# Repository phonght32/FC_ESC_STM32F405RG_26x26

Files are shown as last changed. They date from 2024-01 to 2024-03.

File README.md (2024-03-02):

# FC_ESC_STM32F405RG_26x26

### 1. Overview

All-in-One (AIO) circuit for quadcopter. STM32F405 is the main controller for FC and EFM8BB21 is the main controller for ESC. Screw hole dimension is 26x26 mm that compatible for almost tiny drone frame. 

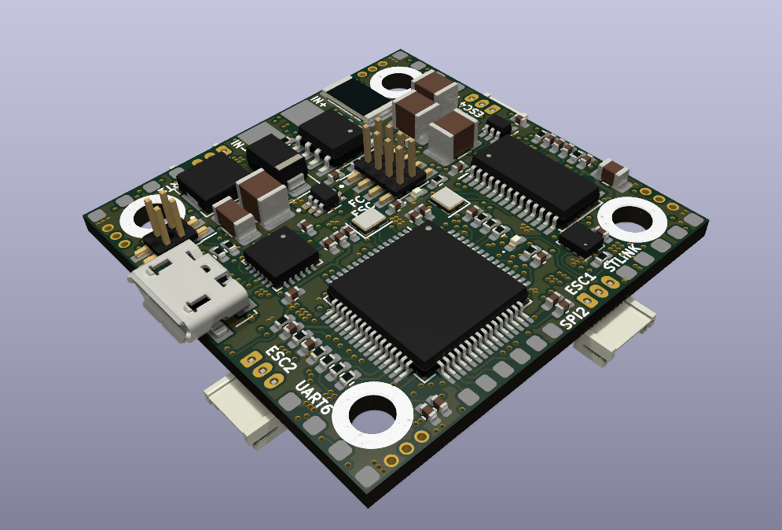
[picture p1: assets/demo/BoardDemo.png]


Everything about this board: Schematic, PCB gerber and BOM are free to distribute under open-source license for users.

### 2. Specifications

| Items | Specifications |
| --- | --- |
| Power supply | Pin LiPo 2-4 cell |
| Microcontroller | STM32F405RGT6 / 32-bit ARM Cortex-M4 with FPU(168MHz, 225DMIPS) |
| Sensors | MPU6000 (3 axis gyroscope, 3 axis accelerometer) <br />BMP280 (barometer)<br />INA186 (current) |
| Programmer | JTAG/SWD connector |
| Communicaton Ports  | UART x 4<br />I2C x 1<br />SPI x 1 |
| OSD | Built-in AT7456 |
| LEDs and Buttons | LED RED: 3V3 power on<br />LED BLUE: User status |
| Output power source | TPS5430 5V@5A<br />RT9013 3V3@500mA |
| Dimensions | 34 x34 mm<br />Screw hole 26 x 26 mm |

**NOTE:**

This board use jumper to select 5V power source and to enable 3V3 power supply.

### 3. Layout / Pin map

| Function | Pin |
| --- | --- |
| UART1 | PA9: TX<br />PA10: RX |
| UART3 | PB10: TX<br />PB11: RX |
| UART4 | PA0: TX<br />PA1: RX |
| UART6 | PC6: TX<br />PC7: RX |
| SPI2 | PB12: CS<br />PB13: CLK<br />PB14: MISO<br />PB15: MOSI |
| I2C2 | PB10: SCL<br />PB11: SDA |
| LED | LED status: PB7<br />LED strip: PB6 |
| BUZZER | PC13 |
| USB Port | D-: PA11<br />D+: PA12 |
| Measurement | Current sens: PC1<br />Voltage sens: PC2<br />USB voltage sens: PC5 |

### 4. Hardware design

#### Schematic

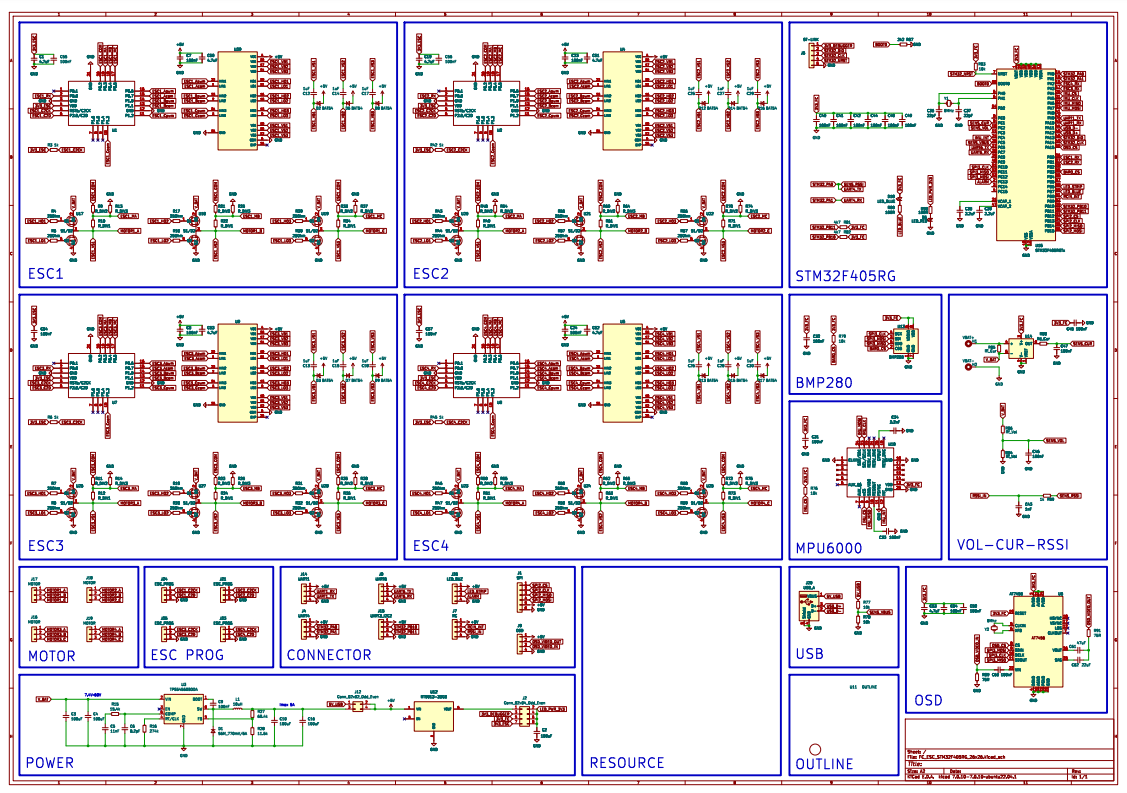
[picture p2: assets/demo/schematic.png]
schematic


#### PCB F.Cu

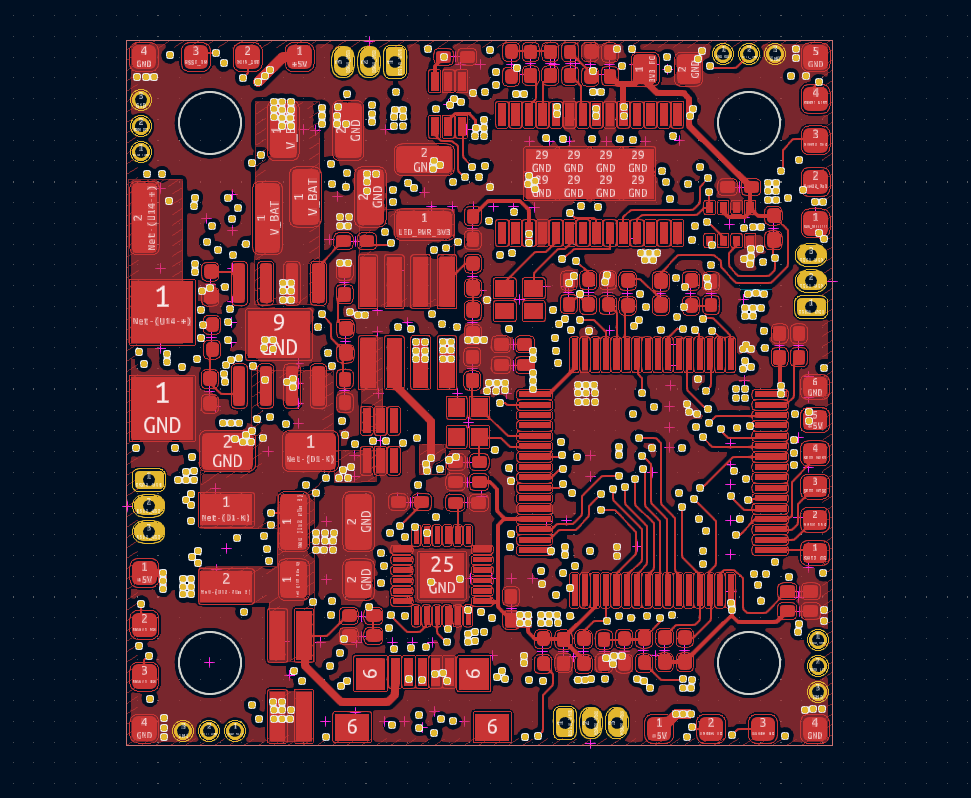
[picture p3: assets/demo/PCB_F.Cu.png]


#### PCB In1.Cu

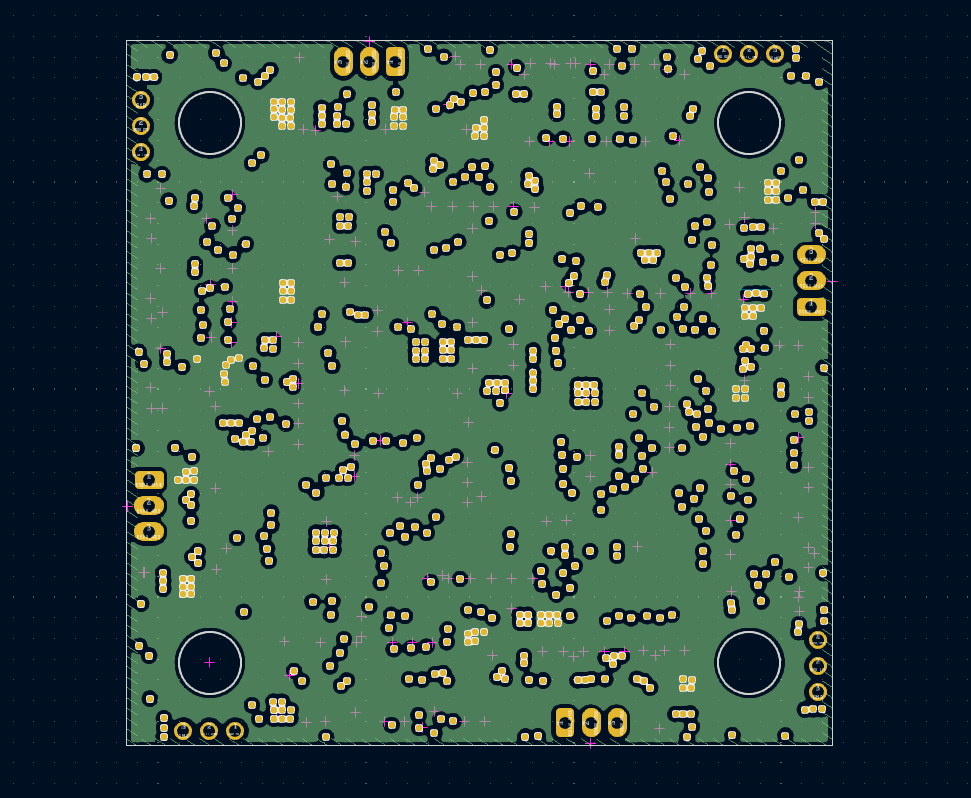
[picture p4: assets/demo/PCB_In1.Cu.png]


#### PCB In2.Cu

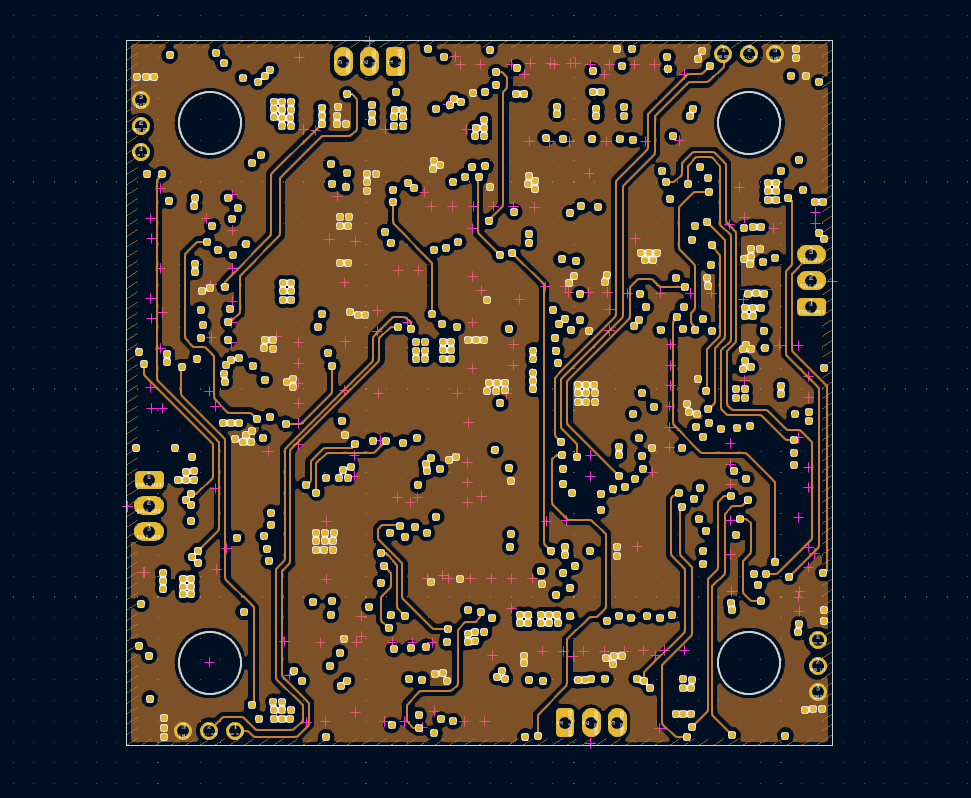
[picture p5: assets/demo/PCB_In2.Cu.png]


#### PCB In3.Cu

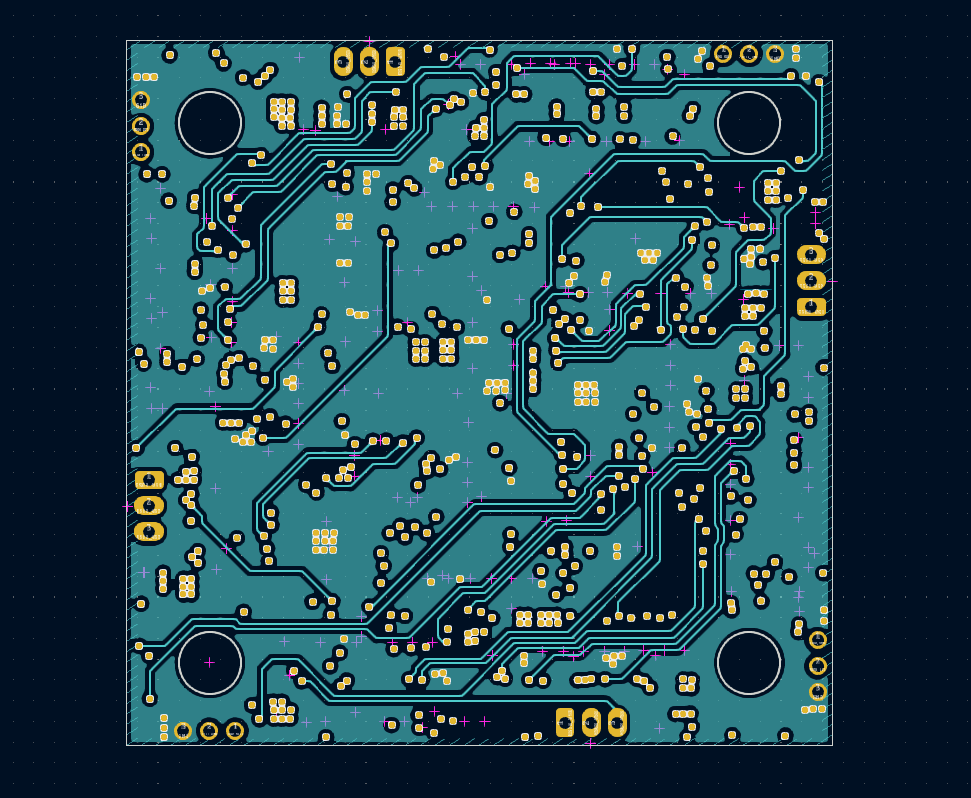
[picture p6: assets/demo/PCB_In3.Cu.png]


#### PCB In4.Cu

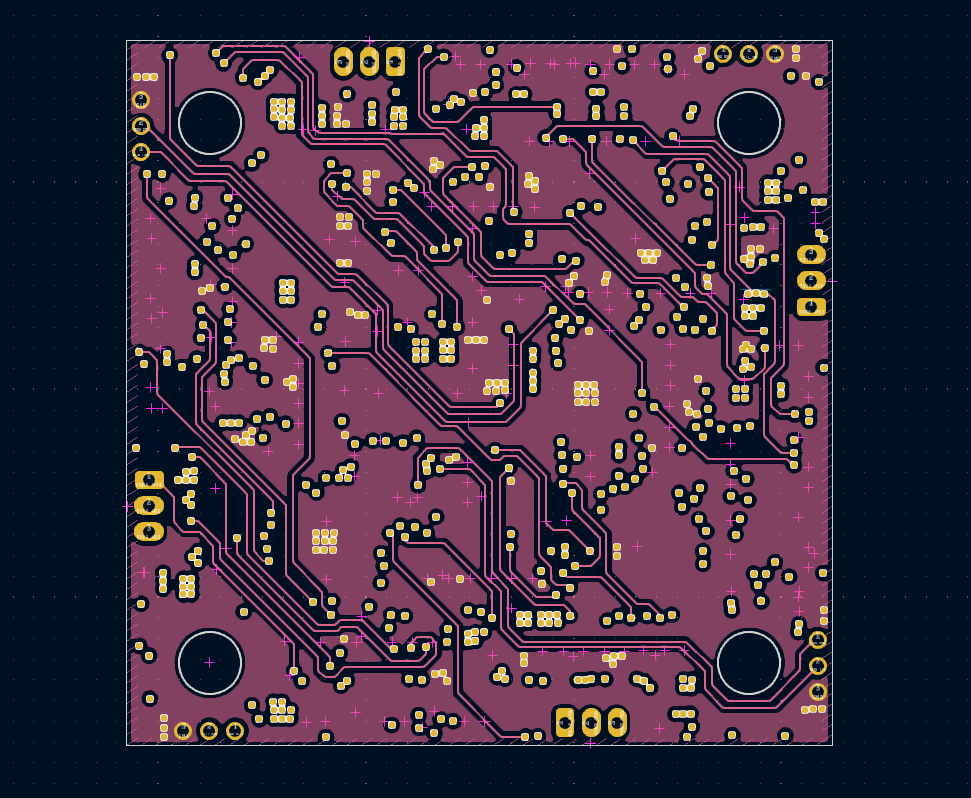
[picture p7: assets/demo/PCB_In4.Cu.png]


#### PCB In5.Cu

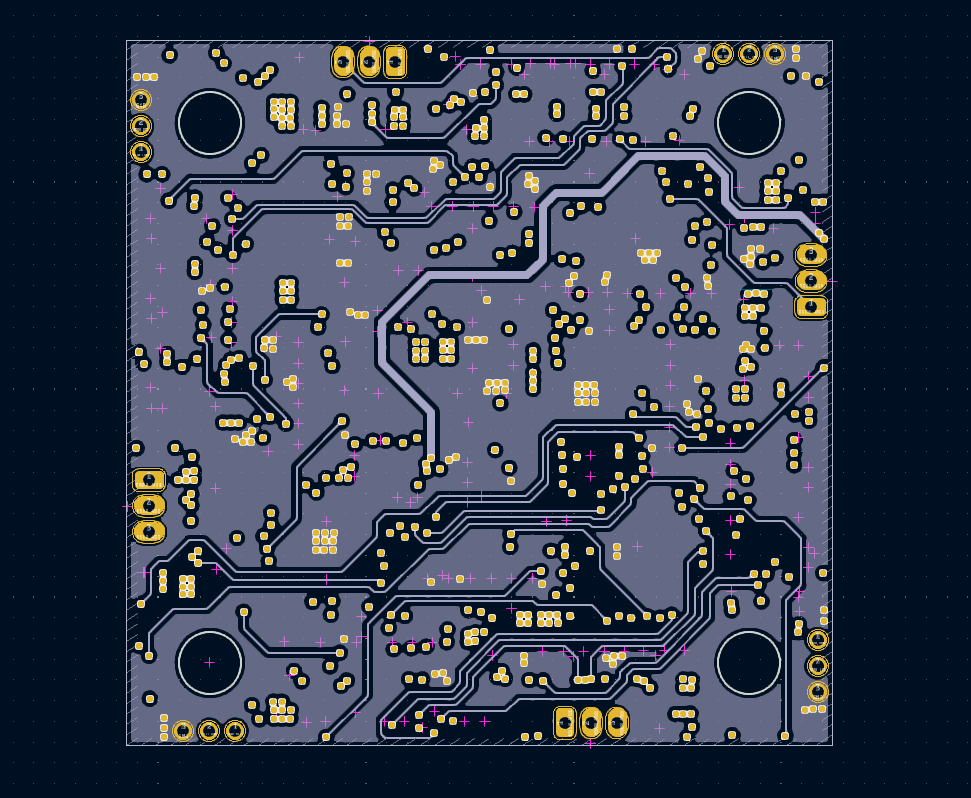
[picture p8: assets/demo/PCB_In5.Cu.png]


#### PCB In6.Cu

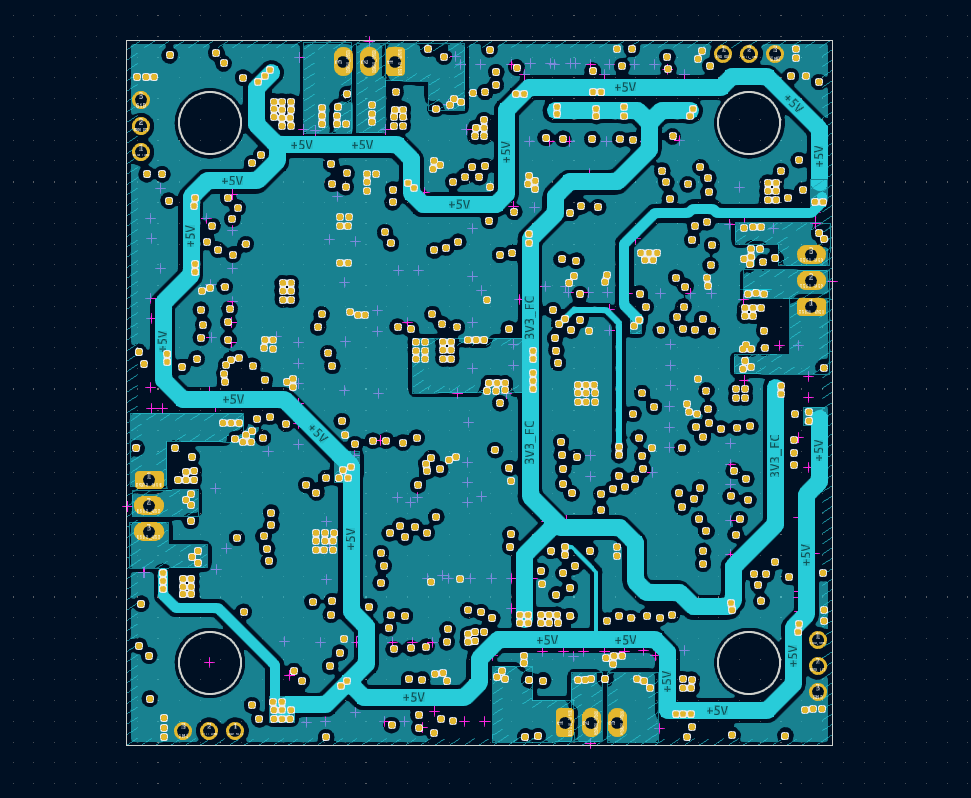
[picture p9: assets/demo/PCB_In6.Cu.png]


#### PCB B.Cu

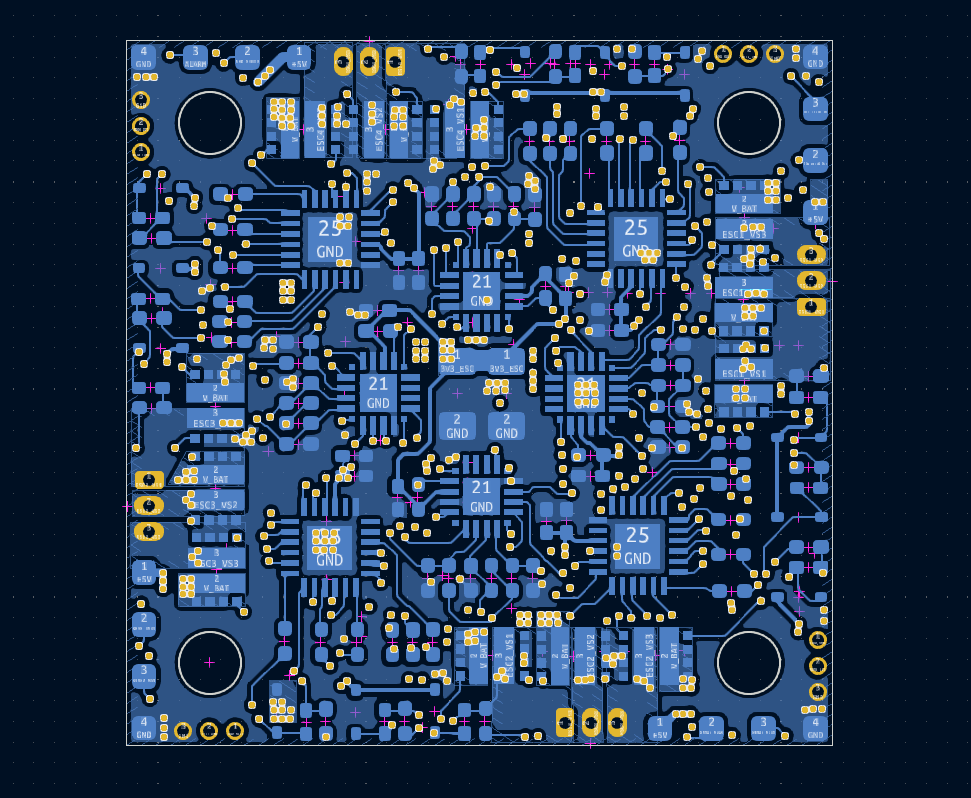
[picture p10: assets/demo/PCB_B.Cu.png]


#### Dimension

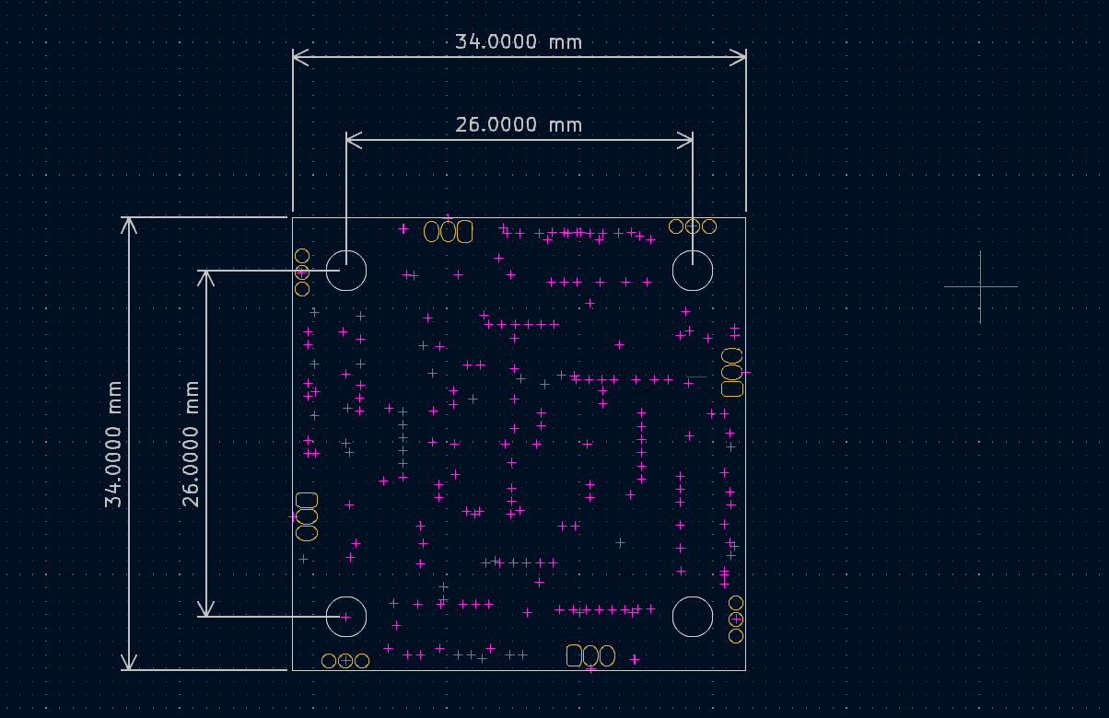
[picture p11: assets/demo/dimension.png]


#### 3D Top

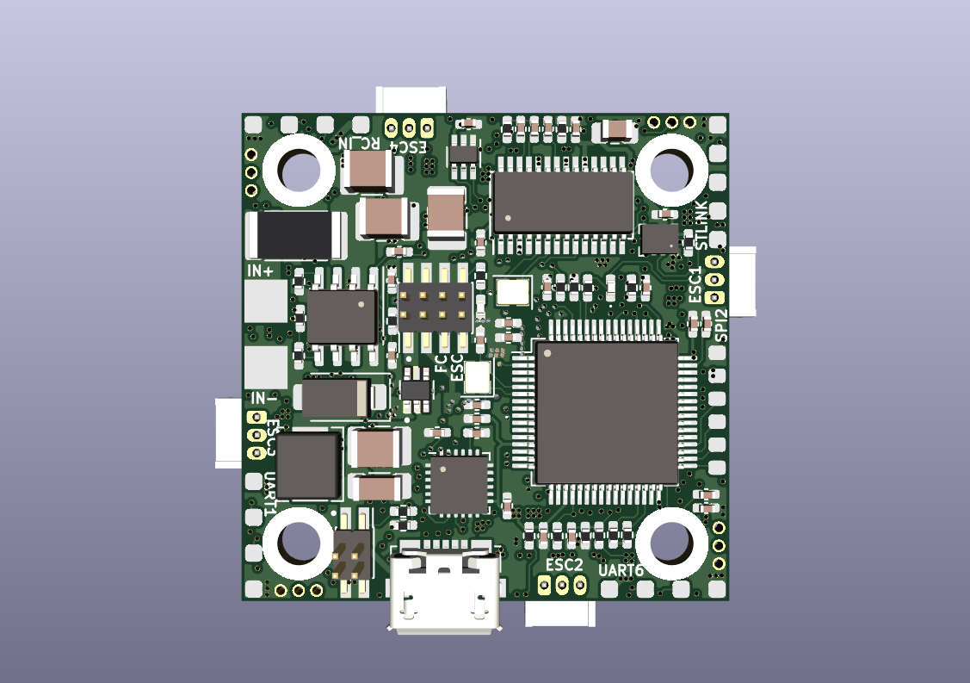
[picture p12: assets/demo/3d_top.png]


#### 3D Bot

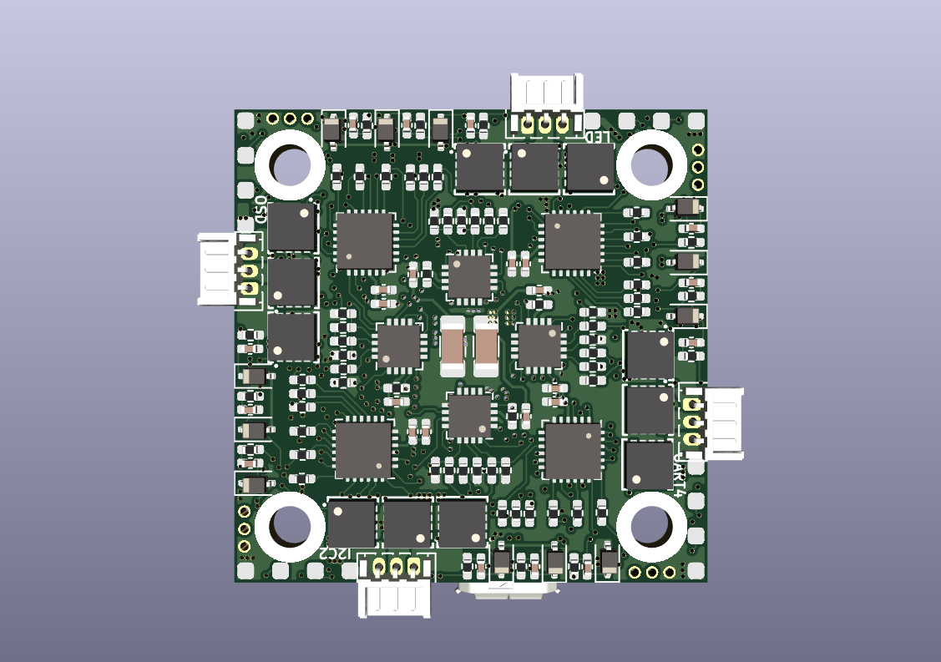
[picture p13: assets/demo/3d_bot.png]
3d_bot


### 5. Bill of Materials (BOM)

[Download.](assets/BOM/FC_ESC_STM32F405RG_26x26.xlsx)

### 6. Gerber

[Download.](assets/gerber_FC_ESC_STM32F405RG_26x26_v1_0.zip)

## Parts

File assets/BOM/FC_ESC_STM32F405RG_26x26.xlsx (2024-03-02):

Reference | Value | Footprint | Qty
C1,C19 | 4.7uF | Capacitor_SMD:C_1206_3216Metric_Pad1.33x1.80mm_HandSolder | 2
C2,C3,C4,C10 | 100uF | Capacitor_SMD:C_1210_3225Metric_Pad1.33x2.70mm_HandSolder | 4
C5 | 11nF | Capacitor_SMD:C_0402_1005Metric_Pad0.74x0.62mm_HandSolder | 1
C6 | 8.2pF | Capacitor_SMD:C_0402_1005Metric_Pad0.74x0.62mm_HandSolder | 1
C7,C8,C9,C23,C24,C31,C32,C33,C40,C41,C42,C44,C45,C46,C47,C48,C49,C54,C55,C56,C57,C59,C60,C64 | 100nF | Capacitor_SMD:C_0402_1005Metric_Pad0.74x0.62mm_HandSolder | 24
C12,C13,C14,C15,C17,C18,C25,C26,C27,C28,C29,C30 | 1uF | Capacitor_SMD:C_0402_1005Metric_Pad0.74x0.62mm_HandSolder | 12
C16 | 100uF | Capacitor_SMD:C_1206_3216Metric_Pad1.33x1.80mm_HandSolder | 1
C34 | 2.2nF | Capacitor_SMD:C_0402_1005Metric_Pad0.74x0.62mm_HandSolder | 1
C36,C37 | 22pF | Capacitor_SMD:C_0402_1005Metric_Pad0.74x0.62mm_HandSolder | 2
C38,C39 | 2.2uF | Capacitor_SMD:C_0402_1005Metric_Pad0.74x0.62mm_HandSolder | 2
C43 | 1nF | Capacitor_SMD:C_0402_1005Metric_Pad0.74x0.62mm_HandSolder | 1
C50,C51,C52,C53 | 4.7uF | Capacitor_SMD:C_0402_1005Metric_Pad0.74x0.62mm_HandSolder | 4
C61 | 47uF | Capacitor_SMD:C_0402_1005Metric_Pad0.74x0.62mm_HandSolder | 1
C62 | 22uF | Capacitor_SMD:C_0402_1005Metric_Pad0.74x0.62mm_HandSolder | 1
C63 | 4.7uF | Capacitor_SMD:C_0805_2012Metric_Pad1.18x1.45mm_HandSolder | 1
D1 | S6M_770mV/6A | Diode_SMD:D_SMA | 1
D2,D3,D6,D7,D8,D9,D12,D13,D14,D15,D16,D17 | BAT54 | Diode_SMD:D_SOD-323 | 12
D5 | LED_RED | LED_SMD:LED_0402_1005Metric_Pad0.77x0.64mm_HandSolder | 1
D18 | LED_BLUE | LED_SMD:LED_0402_1005Metric_Pad0.77x0.64mm_HandSolder | 1
H1 | VBAT+ | Proj_footprint:MoutingPad | 1
H2 | VBAT- | Proj_footprint:MoutingPad | 1
J1 | SPI | Proj_footprint:MountingPad_1x6 | 1
J2 | Conn_02x04_Odd_Even | Proj_footprint:PinHeader_2x04_P1.27mm_Vertical_SMD | 1
J4 | UART4 | Proj_footprint:MountingPad_1x4 | 1
J5 | ST-LINK | Proj_footprint:STLINK_Port | 1
J7 | RC | Proj_footprint:MountingPad_1x4 | 1
J8 | UART6 | Proj_footprint:MountingPad_1x4 | 1
J9 | OSD | Proj_footprint:MountingPad_1x4 | 1
J12 | Conn_02x02_Odd_Even | Proj_footprint:PinHeader_2x02_P1.27mm_Vertical_SMD | 1
J14 | UART1 | Proj_footprint:MountingPad_1x4 | 1
J15 | UART3_I2C2 | Proj_footprint:MountingPad_1x4 | 1
J16,J17,J18,J19 | MOTOR | Proj_footprint:Hirose_DF13-03P-1.25DS_1x03_P1.25mm_Horizontal | 4
J20 | USB_A | Proj_footprint:USB_Micro-B_SMD | 1
J21,J23,J24,J25 | ESC_PROG | Proj_footprint:ESC_Program | 4
J26 | LED_BUZ | Proj_footprint:MountingPad_1x4 | 1
L1 | 10uH | Proj_footprint:Inductor | 1
R3,R6,R42,R45,R89 | 1k | Resistor_SMD:R_0402_1005Metric_Pad0.72x0.64mm_HandSolder | 5
R4,R5,R7,R8,R17,R18,R19,R20,R29,R30,R31,R32,R43,R44,R46,R47,R56,R57,R58,R59,R66,R67,R68,R69 | 25Ohm | Resistor_SMD:R_0402_1005Metric_Pad0.72x0.64mm_HandSolder | 24
R9,R11,R21,R23,R33,R35,R48,R50,R60,R62,R70,R72 | R_DIV2 | Resistor_SMD:R_0402_1005Metric_Pad0.72x0.64mm_HandSolder | 12
R10,R12,R22,R24,R34,R36,R49,R51,R61,R63,R71,R73 | R_DIV1 | Resistor_SMD:R_0402_1005Metric_Pad0.72x0.64mm_HandSolder | 12
R13,R14,R25,R26,R37,R38,R54,R55,R64,R65,R74,R75 | R_DIV3 | Resistor_SMD:R_0402_1005Metric_Pad0.72x0.64mm_HandSolder | 12
R15 | 15.4k | Resistor_SMD:R_0402_1005Metric_Pad0.72x0.64mm_HandSolder | 1
R16 | 274k | Resistor_SMD:R_0402_1005Metric_Pad0.72x0.64mm_HandSolder | 1
R27 | 60.4k | Resistor_SMD:R_0402_1005Metric_Pad0.72x0.64mm_HandSolder | 1
R28 | 11.5k | Resistor_SMD:R_0402_1005Metric_Pad0.72x0.64mm_HandSolder | 1
R39,R91 | 75R | Resistor_SMD:R_0402_1005Metric_Pad0.72x0.64mm_HandSolder | 2
R76,R77,R78,R79,R83 | 10k | Resistor_SMD:R_0402_1005Metric_Pad0.72x0.64mm_HandSolder | 5
R80,R93 | 100R | Resistor_SMD:R_0402_1005Metric_Pad0.72x0.64mm_HandSolder | 2
R81,R82 | 4k7 | Resistor_SMD:R_0402_1005Metric_Pad0.72x0.64mm_HandSolder | 2
R84 | Ri_Vol | Resistor_SMD:R_0402_1005Metric_Pad0.72x0.64mm_HandSolder | 1
R85 | Ri_Cur | Resistor_SMD:R_2512_6332Metric | 1
R86 | Rf_Vol | Resistor_SMD:R_0402_1005Metric_Pad0.72x0.64mm_HandSolder | 1
R87 | 2k2 | Resistor_SMD:R_0402_1005Metric_Pad0.72x0.64mm_HandSolder | 1
R88 | Rd_Cur | Resistor_SMD:R_0402_1005Metric_Pad0.72x0.64mm_HandSolder | 1
U1,U2,U7,U8 | EFM8BB21 | Proj_footprint:QFN-20-1EP_3x3mm_P0.5mm_EP1.8x1.8mm | 4
U3 | TPS54560BDDA | Proj_footprint:SOIC-8-1EP_3.9x4.9mm_P1.27mm_EP2.29x3mm | 1
U4,U5,U9,U29 | FD6288Q | Proj_footprint:QFN-24-1EP_4x4mm_P0.5mm_EP2.15x2.15mm | 4
U6 | AT7456 | Package_SO:TSSOP-28-1EP_4.4x9.7mm_P0.65mm | 1
U10 | MPU6000 | Proj_footprint:QFN-24-1EP_4x4mm_P0.5mm_EP2.15x2.15mm | 1
U11 | OUTLINE | Proj_footprint:Board_Outline | 1
U12 | RT9013-33GB | Proj_footprint:SOT65P210X110-6N | 1
U13 | BMP280 | Package_LGA:Bosch_LGA-8_2x2.5mm_P0.65mm_ClockwisePinNumbering | 1
U14 | INA186 | Package_TO_SOT_SMD:Texas_R-PDSO-G6 | 1
U15 | STM32F405RGTx | Package_QFP:LQFP-64_10x10mm_P0.5mm | 1
U17,U18,U19,U20,U21,U22,U23,U24,U25,U26,U27,U28 | SIZ200DT | Proj_footprint:SIZ200DT | 12
Y1 | 8MHz | Proj_footprint:Crystal_SMD_2016-4Pin_2.0x1.6mm | 1
Y2 | 8Mhz | Proj_footprint:Crystal_SMD_2016-4Pin_2.0x1.6mm | 1

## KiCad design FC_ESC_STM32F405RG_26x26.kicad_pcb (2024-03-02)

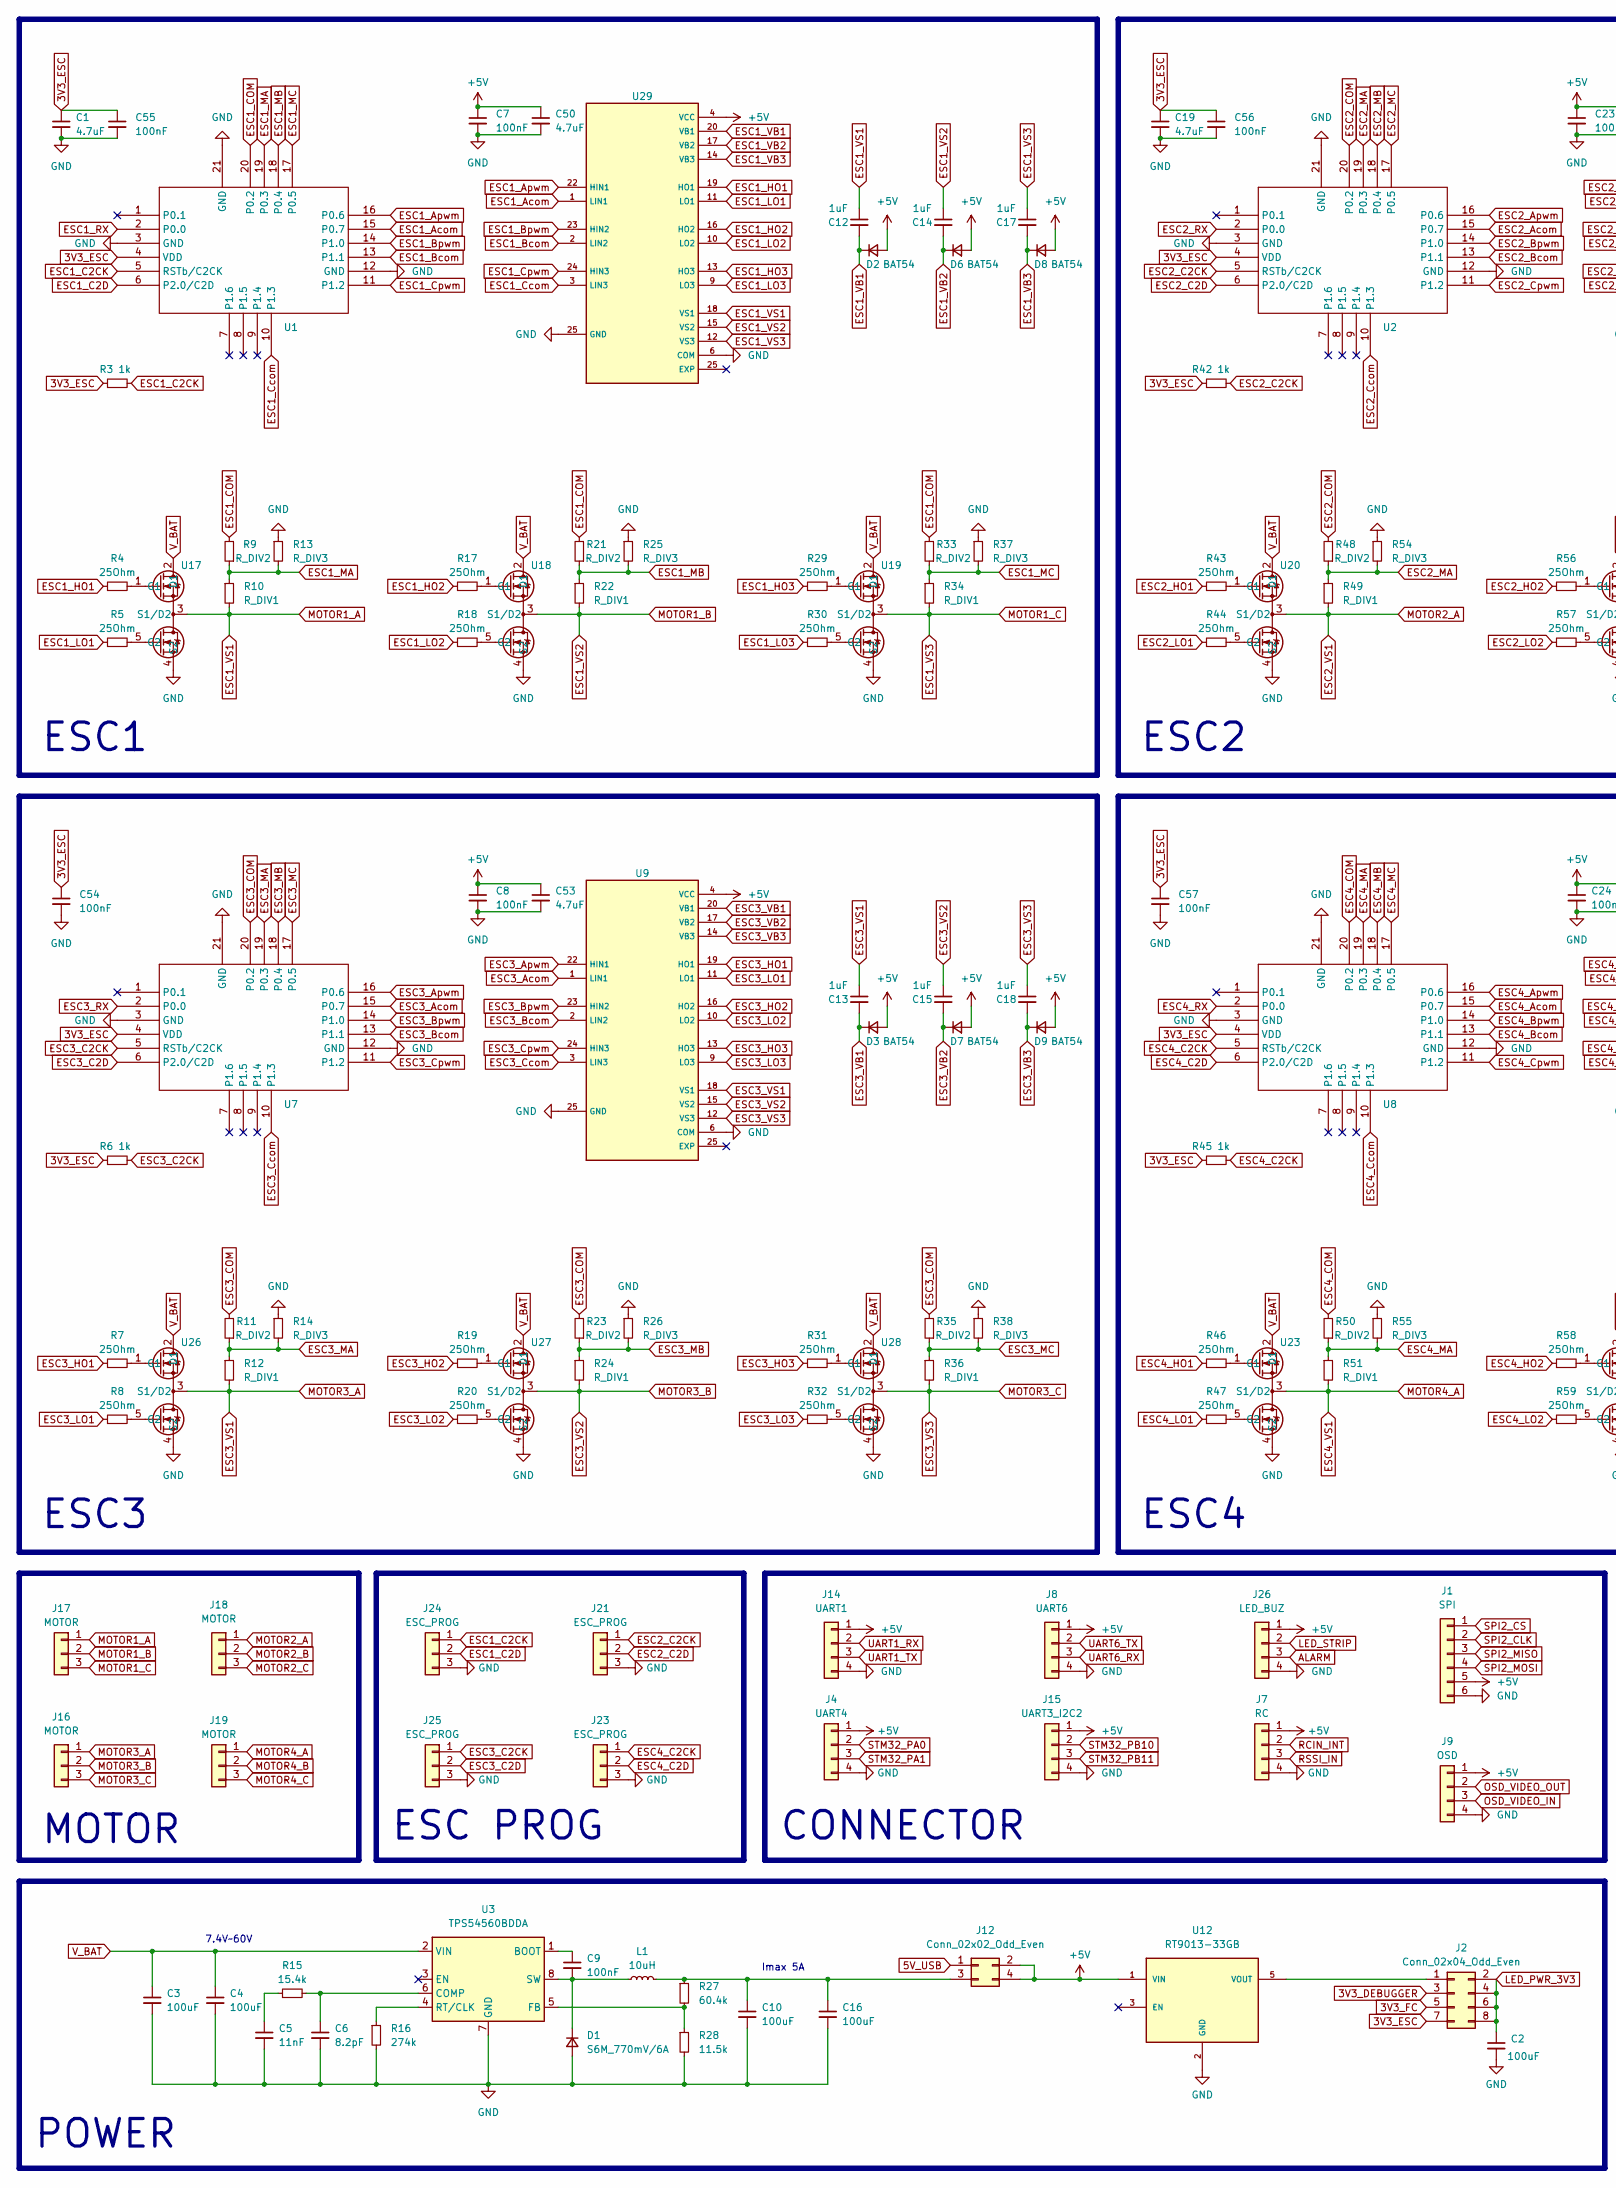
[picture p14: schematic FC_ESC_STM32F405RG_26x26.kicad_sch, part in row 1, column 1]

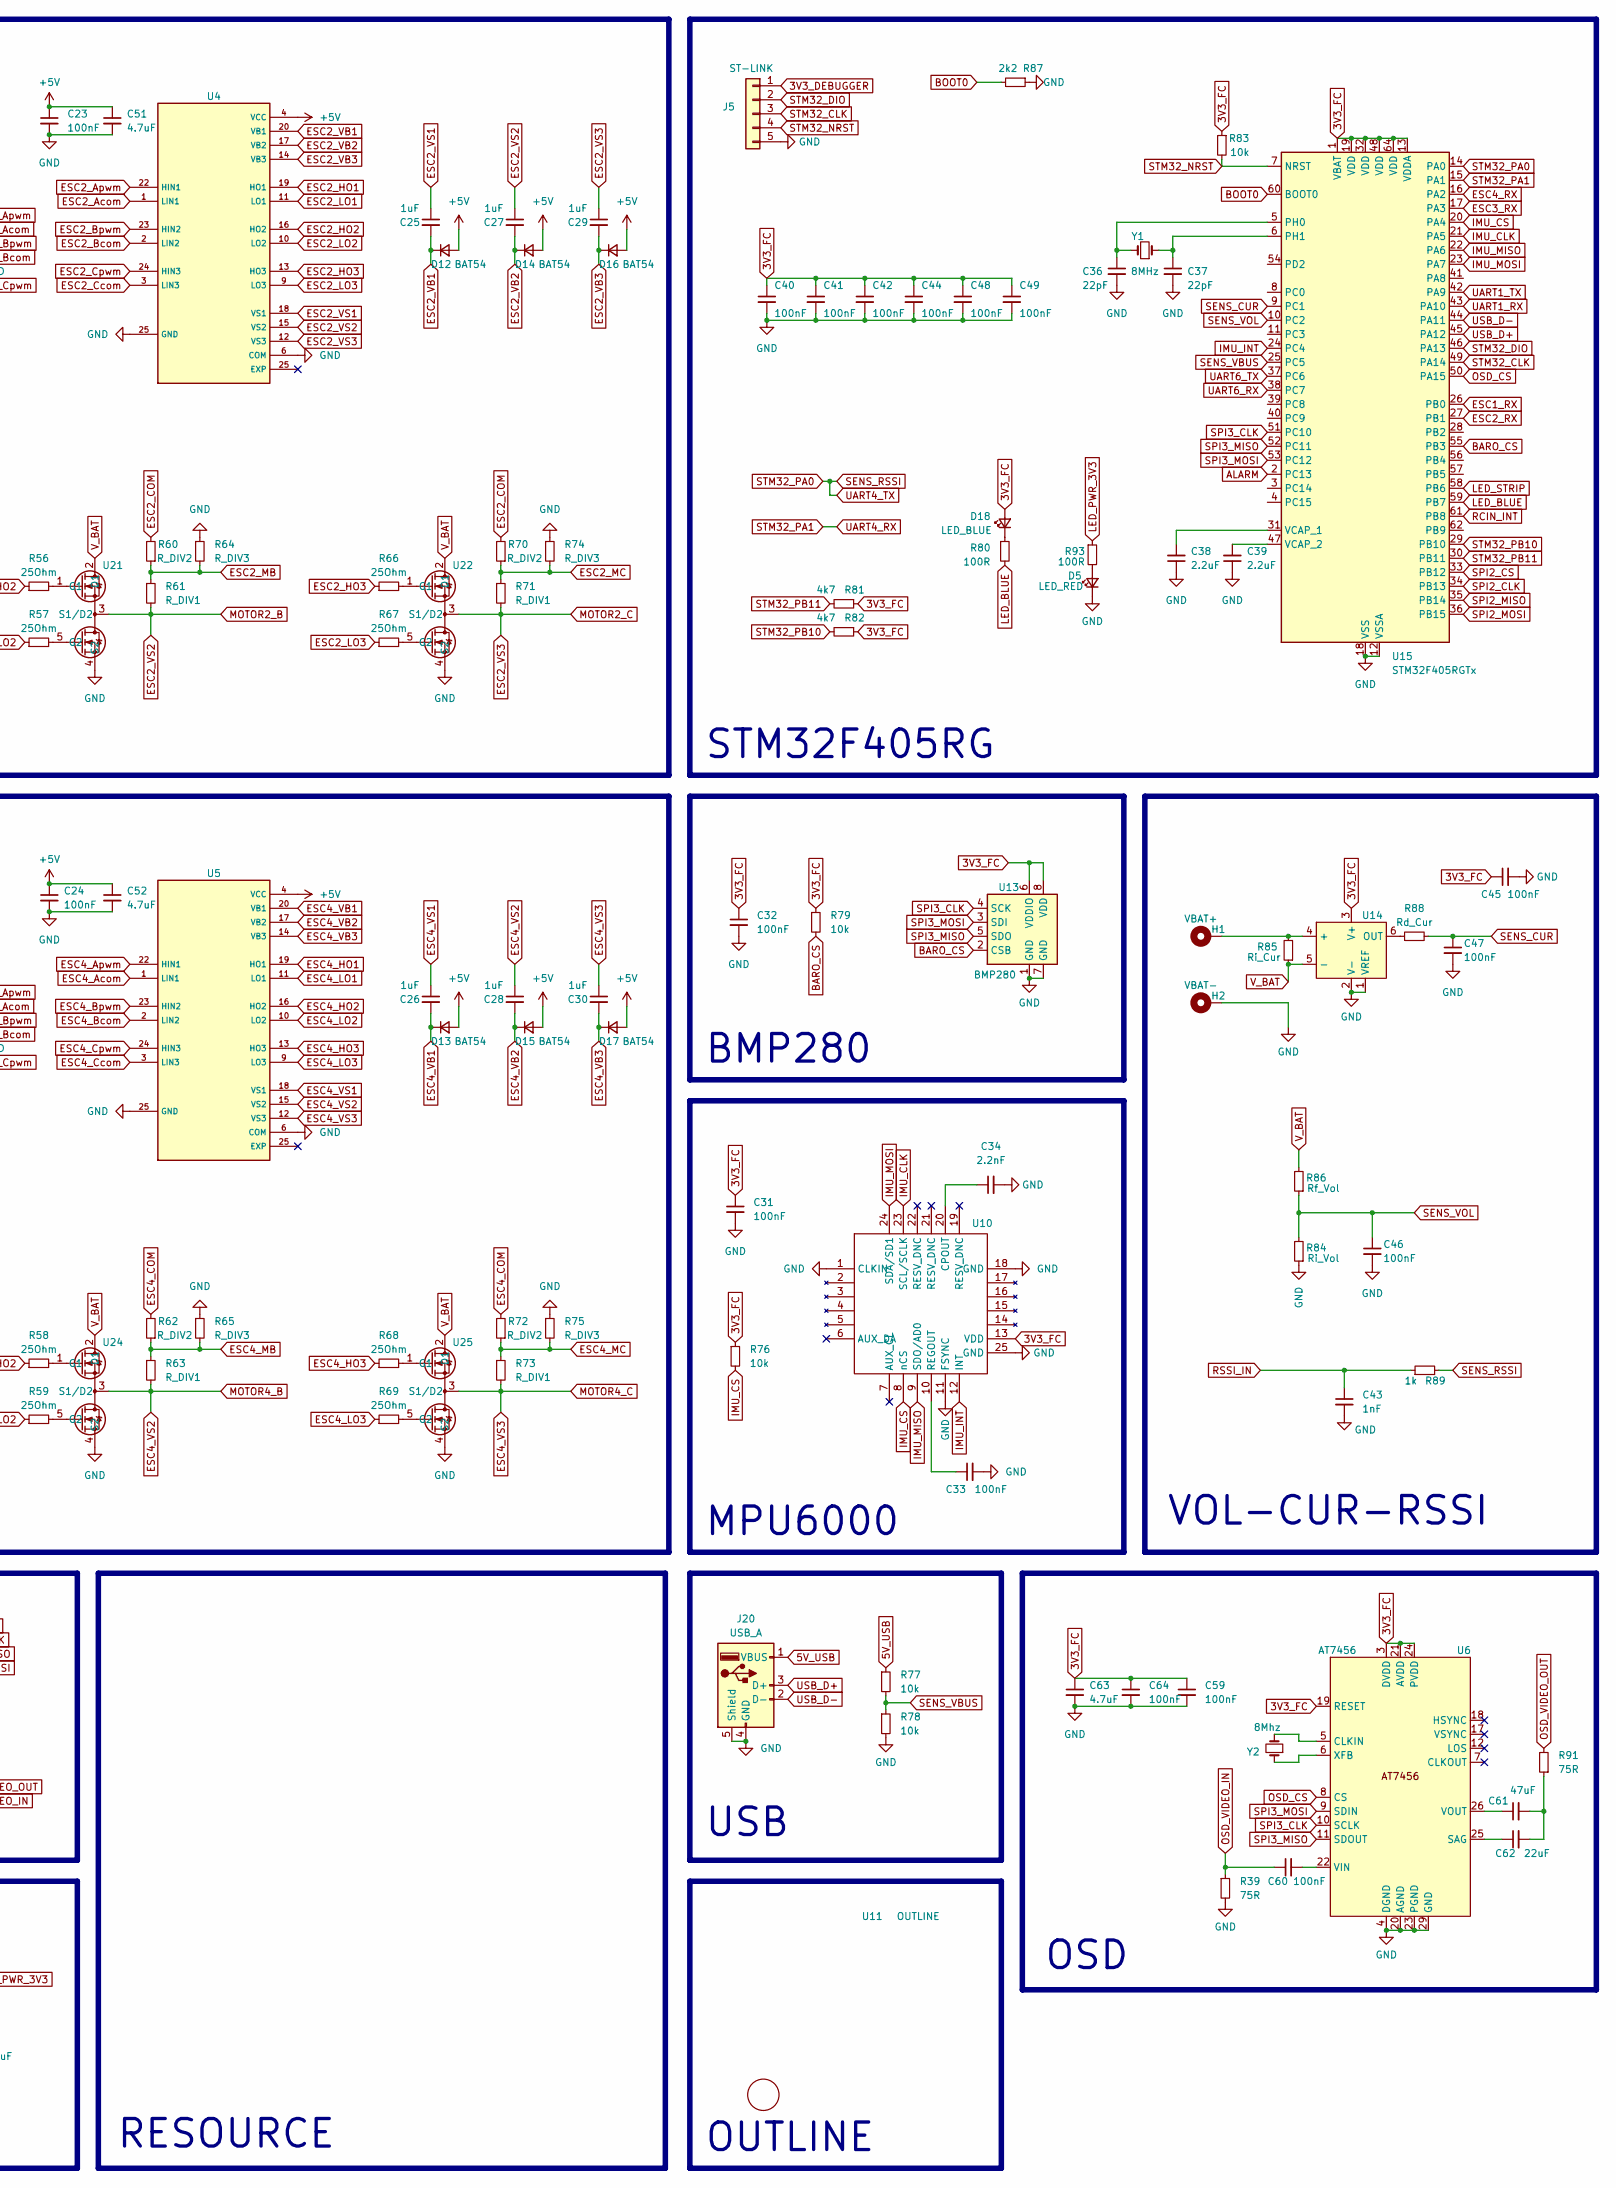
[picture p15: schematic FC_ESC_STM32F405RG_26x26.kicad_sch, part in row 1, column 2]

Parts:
C1, C19: 4.7uF; C_1206_3216Metric_Pad1.33x1.80mm_HandSolder
C2, C3, C4, C10: 100uF; C_1210_3225Metric_Pad1.33x2.70mm_HandSolder
C5: 11nF; C_0402_1005Metric_Pad0.74x0.62mm_HandSolder
C6: 8.2pF; C_0402_1005Metric_Pad0.74x0.62mm_HandSolder
C7, C8, C9, C23, C24, C31, C32, C33, C40, C41, C42, C44, C45, C46, C47, C48, C49, C54, C55, C56, C57, C59, C60, C64: 100nF; C_0402_1005Metric_Pad0.74x0.62mm_HandSolder
C12, C13, C14, C15, C17, C18, C25, C26, C27, C28, C29, C30: 1uF; C_0402_1005Metric_Pad0.74x0.62mm_HandSolder
C16: 100uF; C_1206_3216Metric_Pad1.33x1.80mm_HandSolder
C34: 2.2nF; C_0402_1005Metric_Pad0.74x0.62mm_HandSolder
C36, C37: 22pF; C_0402_1005Metric_Pad0.74x0.62mm_HandSolder
C38, C39: 2.2uF; C_0402_1005Metric_Pad0.74x0.62mm_HandSolder
C43: 1nF; C_0402_1005Metric_Pad0.74x0.62mm_HandSolder
C50, C51, C52, C53: 4.7uF; C_0402_1005Metric_Pad0.74x0.62mm_HandSolder
C61: 47uF; C_0402_1005Metric_Pad0.74x0.62mm_HandSolder
C62: 22uF; C_0402_1005Metric_Pad0.74x0.62mm_HandSolder
C63: 4.7uF; C_0805_2012Metric_Pad1.18x1.45mm_HandSolder
D1: S6M_770mV/6A; D_SMA
D2, D3, D6, D7, D8, D9, D12, D13, D14, D15, D16, D17: BAT54; D_SOD-323
D5: LED_RED; LED_0402_1005Metric_Pad0.77x0.64mm_HandSolder
D18: LED_BLUE; LED_0402_1005Metric_Pad0.77x0.64mm_HandSolder
H1: VBAT+; MoutingPad
H2: VBAT-; MoutingPad
J1: SPI; MountingPad_1x6
J2: Conn_02x04_Odd_Even; PinHeader_2x04_P1.27mm_Vertical_SMD
J4: UART4; MountingPad_1x4
J5: ST-LINK; STLINK_Port
J7: RC; MountingPad_1x4
J8: UART6; MountingPad_1x4
J9: OSD; MountingPad_1x4
J12: Conn_02x02_Odd_Even; PinHeader_2x02_P1.27mm_Vertical_SMD
J14: UART1; MountingPad_1x4
J15: UART3_I2C2; MountingPad_1x4
J16, J17, J18, J19: MOTOR; Hirose_DF13-03P-1.25DS_1x03_P1.25mm_Horizontal
J20: USB_A; USB_Micro-B_SMD
J21, J23, J24, J25: ESC_PROG; ESC_Program
J26: LED_BUZ; MountingPad_1x4
L1: 10uH; Inductor
R3, R6, R42, R45, R89: 1k; R_0402_1005Metric_Pad0.72x0.64mm_HandSolder
R4, R5, R7, R8, R17, R18, R19, R20, R29, R30, R31, R32, R43, R44, R46, R47, R56, R57, R58, R59, R66, R67, R68, R69: 25Ohm; R_0402_1005Metric_Pad0.72x0.64mm_HandSolder
R9, R11, R21, R23, R33, R35, R48, R50, R60, R62, R70, R72: R_DIV2; R_0402_1005Metric_Pad0.72x0.64mm_HandSolder
R10, R12, R22, R24, R34, R36, R49, R51, R61, R63, R71, R73: R_DIV1; R_0402_1005Metric_Pad0.72x0.64mm_HandSolder
R13, R14, R25, R26, R37, R38, R54, R55, R64, R65, R74, R75: R_DIV3; R_0402_1005Metric_Pad0.72x0.64mm_HandSolder
R15: 15.4k; R_0402_1005Metric_Pad0.72x0.64mm_HandSolder
R16: 274k; R_0402_1005Metric_Pad0.72x0.64mm_HandSolder
R27: 60.4k; R_0402_1005Metric_Pad0.72x0.64mm_HandSolder
R28: 11.5k; R_0402_1005Metric_Pad0.72x0.64mm_HandSolder
R39, R91: 75R; R_0402_1005Metric_Pad0.72x0.64mm_HandSolder
R76, R77, R78, R79, R83: 10k; R_0402_1005Metric_Pad0.72x0.64mm_HandSolder
R80, R93: 100R; R_0402_1005Metric_Pad0.72x0.64mm_HandSolder
R81, R82: 4k7; R_0402_1005Metric_Pad0.72x0.64mm_HandSolder
R84: Ri_Vol; R_0402_1005Metric_Pad0.72x0.64mm_HandSolder
R85: Ri_Cur; R_2512_6332Metric
R86: Rf_Vol; R_0402_1005Metric_Pad0.72x0.64mm_HandSolder
R87: 2k2; R_0402_1005Metric_Pad0.72x0.64mm_HandSolder
R88: Rd_Cur; R_0402_1005Metric_Pad0.72x0.64mm_HandSolder
U1, U2, U7, U8: QFN-20-1EP_3x3mm_P0.5mm_EP1.8x1.8mm
U3: TPS54560BDDA; SOIC-8-1EP_3.9x4.9mm_P1.27mm_EP2.29x3mm
U4, U5, U9, U10, U29: QFN-24-1EP_4x4mm_P0.5mm_EP2.15x2.15mm
U6: AT7456; TSSOP-28-1EP_4.4x9.7mm_P0.65mm
U11: OUTLINE; Board_Outline
U12: RT9013-33GB; SOT65P210X110-6N; PARTREV Aprill 2011
U13: BMP280; Bosch_LGA-8_2x2.5mm_P0.65mm_ClockwisePinNumbering
U14: Texas_R-PDSO-G6
U15: STM32F405RGTx; LQFP-64_10x10mm_P0.5mm
U17, U18, U19, U20, U21, U22, U23, U24, U25, U26, U27, U28: SIZ200DT
Y1: 8MHz; Crystal_SMD_2016-4Pin_2.0x1.6mm
Y2: 8Mhz; Crystal_SMD_2016-4Pin_2.0x1.6mm

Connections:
3V3_DEBUGGER: J2.3, J5.1
3V3_ESC: C1.1, C19.1, C54.1, C55.1, C56.1, C57.1, J2.7, R3.1, R6.1, R42.1, R45.1, U1.4 (VDD), U2.4 (VDD), U7.4 (VDD), U8.4 (VDD)
3V3_FC: C31.1, C32.1, C40.1, C41.1, C42.1, C44.1, C45.1, C48.1, C49.1, C59.1, C63.1, C64.1, D18.2 (A), J2.5, R76.1, R79.1, R81.1, R82.1, R83.1, U6.3 (DVDD), U6.19 (RESET), U6.21 (AVDD), U6.24 (PVDD), U10.13 (VDD), U13.6 (VDDIO), U13.8 (VDD), U14.3 (V+), U15.1 (VBAT), U15.13 (VDDA), U15.19 (VDD), U15.32 (VDD), U15.48 (VDD), U15.64 (VDD)
5V_USB: J12.1, J20.1 (VBUS), R77.1
+5V: C7.1, C8.1, C23.1, C24.1, C50.1, C51.1, C52.1, C53.1, D2.2 (A), D3.2 (A), D6.2 (A), D7.2 (A), D8.2 (A), D9.2 (A), D12.2 (A), D13.2 (A), D14.2 (A), D15.2 (A), D16.2 (A), D17.2 (A), J1.5, J4.1, J7.1, J8.1, J9.1, J12.2, J12.4, J14.1, J15.1, J26.1, U4.4 (VCC), U5.4 (VCC), U9.4 (VCC), U12.1 (VIN), U29.4 (VCC)
ALARM: J26.3, U15.2 (PC13)
BARO_CS: R79.2, U13.2 (CSB), U15.55 (PB3)
BOOT0: R87.2, U15.60 (BOOT0)
ESC1_Acom: U1.15 (P0.7), U29.1 (LIN1)
ESC1_Apwm: U1.16 (P0.6), U29.22 (HIN1)
ESC1_Bcom: U1.13 (P1.1), U29.2 (LIN2)
ESC1_Bpwm: U1.14 (P1.0), U29.23 (HIN2)
ESC1_C2CK: J24.1, R3.2, U1.5 (RSTb/C2CK)
ESC1_C2D: J24.2, U1.6 (P2.0/C2D)
ESC1_COM: R9.2, R21.2, R33.2, U1.20 (P0.2)
ESC1_Ccom: U1.10 (P1.3), U29.3 (LIN3)
ESC1_Cpwm: U1.11 (P1.2), U29.24 (HIN3)
ESC1_HO1: R4.1, U29.19 (HO1)
ESC1_HO2: R17.1, U29.16 (HO2)
ESC1_HO3: R29.1, U29.13 (HO3)
ESC1_LO1: R5.1, U29.11 (LO1)
ESC1_LO2: R18.1, U29.10 (LO2)
ESC1_LO3: R30.1, U29.9 (LO3)
ESC1_MA: R9.1, R10.1, R13.2, U1.19 (P0.3)
ESC1_MB: R21.1, R22.1, R25.2, U1.18 (P0.4)
ESC1_MC: R33.1, R34.1, R37.2, U1.17 (P0.5)
ESC1_RX: U1.2 (P0.0), U15.26 (PB0)
ESC1_VB1: C12.2, D2.1 (K), U29.20 (VB1)
ESC1_VB2: C14.2, D6.1 (K), U29.17 (VB2)
ESC1_VB3: C17.2, D8.1 (K), U29.14 (VB3)
ESC1_VS1: C12.1, J17.1, R10.2, U17.3 (S1/D2), U29.18 (VS1)
ESC1_VS2: C14.1, J17.2, R22.2, U18.3 (S1/D2), U29.15 (VS2)
ESC1_VS3: C17.1, J17.3, R34.2, U19.3 (S1/D2), U29.12 (VS3)
ESC2_Acom: U2.15 (P0.7), U4.1 (LIN1)
ESC2_Apwm: U2.16 (P0.6), U4.22 (HIN1)
ESC2_Bcom: U2.13 (P1.1), U4.2 (LIN2)
ESC2_Bpwm: U2.14 (P1.0), U4.23 (HIN2)
ESC2_C2CK: J21.1, R42.2, U2.5 (RSTb/C2CK)
ESC2_C2D: J21.2, U2.6 (P2.0/C2D)
ESC2_COM: R48.2, R60.2, R70.2, U2.20 (P0.2)
ESC2_Ccom: U2.10 (P1.3), U4.3 (LIN3)
ESC2_Cpwm: U2.11 (P1.2), U4.24 (HIN3)
ESC2_HO1: R43.1, U4.19 (HO1)
ESC2_HO2: R56.1, U4.16 (HO2)
ESC2_HO3: R66.1, U4.13 (HO3)
ESC2_LO1: R44.1, U4.11 (LO1)
ESC2_LO2: R57.1, U4.10 (LO2)
ESC2_LO3: R67.1, U4.9 (LO3)
ESC2_MA: R48.1, R49.1, R54.2, U2.19 (P0.3)
ESC2_MB: R60.1, R61.1, R64.2, U2.18 (P0.4)
ESC2_MC: R70.1, R71.1, R74.2, U2.17 (P0.5)
ESC2_RX: U2.2 (P0.0), U15.27 (PB1)
ESC2_VB1: C25.2, D12.1 (K), U4.20 (VB1)
ESC2_VB2: C27.2, D14.1 (K), U4.17 (VB2)
ESC2_VB3: C29.2, D16.1 (K), U4.14 (VB3)
ESC2_VS1: C25.1, J18.1, R49.2, U4.18 (VS1), U20.3 (S1/D2)
ESC2_VS2: C27.1, J18.2, R61.2, U4.15 (VS2), U21.3 (S1/D2)
ESC2_VS3: C29.1, J18.3, R71.2, U4.12 (VS3), U22.3 (S1/D2)
ESC3_Acom: U7.15 (P0.7), U9.1 (LIN1)
ESC3_Apwm: U7.16 (P0.6), U9.22 (HIN1)
ESC3_Bcom: U7.13 (P1.1), U9.2 (LIN2)
ESC3_Bpwm: U7.14 (P1.0), U9.23 (HIN2)
ESC3_C2CK: J25.1, R6.2, U7.5 (RSTb/C2CK)
ESC3_C2D: J25.2, U7.6 (P2.0/C2D)
ESC3_COM: R11.2, R23.2, R35.2, U7.20 (P0.2)
ESC3_Ccom: U7.10 (P1.3), U9.3 (LIN3)
ESC3_Cpwm: U7.11 (P1.2), U9.24 (HIN3)
ESC3_HO1: R7.1, U9.19 (HO1)
ESC3_HO2: R19.1, U9.16 (HO2)
ESC3_HO3: R31.1, U9.13 (HO3)
ESC3_LO1: R8.1, U9.11 (LO1)
ESC3_LO2: R20.1, U9.10 (LO2)
ESC3_LO3: R32.1, U9.9 (LO3)
ESC3_MA: R11.1, R12.1, R14.2, U7.19 (P0.3)
ESC3_MB: R23.1, R24.1, R26.2, U7.18 (P0.4)
ESC3_MC: R35.1, R36.1, R38.2, U7.17 (P0.5)
ESC3_RX: U7.2 (P0.0), U15.17 (PA3)
ESC3_VB1: C13.2, D3.1 (K), U9.20 (VB1)
ESC3_VB2: C15.2, D7.1 (K), U9.17 (VB2)
ESC3_VB3: C18.2, D9.1 (K), U9.14 (VB3)
ESC3_VS1: C13.1, J16.1, R12.2, U9.18 (VS1), U26.3 (S1/D2)
ESC3_VS2: C15.1, J16.2, R24.2, U9.15 (VS2), U27.3 (S1/D2)
ESC3_VS3: C18.1, J16.3, R36.2, U9.12 (VS3), U28.3 (S1/D2)
ESC4_Acom: U5.1 (LIN1), U8.15 (P0.7)
ESC4_Apwm: U5.22 (HIN1), U8.16 (P0.6)
ESC4_Bcom: U5.2 (LIN2), U8.13 (P1.1)
ESC4_Bpwm: U5.23 (HIN2), U8.14 (P1.0)
ESC4_C2CK: J23.1, R45.2, U8.5 (RSTb/C2CK)
ESC4_C2D: J23.2, U8.6 (P2.0/C2D)
ESC4_COM: R50.2, R62.2, R72.2, U8.20 (P0.2)
ESC4_Ccom: U5.3 (LIN3), U8.10 (P1.3)
ESC4_Cpwm: U5.24 (HIN3), U8.11 (P1.2)
ESC4_HO1: R46.1, U5.19 (HO1)
ESC4_HO2: R58.1, U5.16 (HO2)
ESC4_HO3: R68.1, U5.13 (HO3)
ESC4_LO1: R47.1, U5.11 (LO1)
ESC4_LO2: R59.1, U5.10 (LO2)
ESC4_LO3: R69.1, U5.9 (LO3)
ESC4_MA: R50.1, R51.1, R55.2, U8.19 (P0.3)
ESC4_MB: R62.1, R63.1, R65.2, U8.18 (P0.4)
ESC4_MC: R72.1, R73.1, R75.2, U8.17 (P0.5)
ESC4_RX: U8.2 (P0.0), U15.16 (PA2)
ESC4_VB1: C26.2, D13.1 (K), U5.20 (VB1)
ESC4_VB2: C28.2, D15.1 (K), U5.17 (VB2)
ESC4_VB3: C30.2, D17.1 (K), U5.14 (VB3)
ESC4_VS1: C26.1, J19.1, R51.2, U5.18 (VS1), U23.3 (S1/D2)
ESC4_VS2: C28.1, J19.2, R63.2, U5.15 (VS2), U24.3 (S1/D2)
ESC4_VS3: C30.1, J19.3, R73.2, U5.12 (VS3), U25.3 (S1/D2)
GND: C1.2, C2.2, C3.2, C4.2, C5.2, C6.2, C7.2, C8.2, C10.2, C16.2, C19.2, C23.2, C24.2, C31.2, C32.2, C33.2, C34.2, C36.2, C37.2, C38.1, C39.1, C40.2, C41.2, C42.2, C43.2, C44.2, C45.2, C46.2, C47.2, C48.2, C49.2, C50.2, C51.2, C52.2, C53.2, C54.2, C55.2, C56.2, C57.2, C59.2, C63.2, C64.2, D1.2 (A), D5.1 (K), H2.1, J1.6, J4.4, J5.5, J7.4, J8.4, J9.4, J14.4, J15.4, J20.4 (GND), J20.5 (Shield), J21.3, J23.3, J24.3, J25.3, J26.4, R13.1, R14.1, R16.2, R25.1, R26.1, R28.2, R37.1, R38.1, R39.2, R54.1, R55.1, R64.1, R65.1, R74.1, R75.1, R78.2, R84.1, R87.1, U1.3 (GND), U1.12 (GND), U1.21 (GND), U2.3 (GND), U2.12 (GND), U2.21 (GND), U3.7 (GND), U3.9 (GND), U4.6 (COM), U4.25 (GND), U5.6 (COM), U5.25 (GND), U6.4 (DGND), U6.20 (AGND), U6.23 (PGND), U6.29 (GND), U7.3 (GND), U7.12 (GND), U7.21 (GND), U8.3 (GND), U8.12 (GND), U8.21 (GND), U9.6 (COM), U9.25 (GND), U10.1 (CLKIN), U10.11 (FSYNC), U10.18 (GND), U10.25 (GND), U12.2 (GND), U13.1 (GND), U13.7 (GND), U14.1 (VREF), U14.2 (V-), U15.12 (VSSA), U15.18 (VSS), U15.63 (VSS), U17.4 (S2), U18.4 (S2), U19.4 (S2), U20.4 (S2), U21.4 (S2), U22.4 (S2), U23.4 (S2), U24.4 (S2), U25.4 (S2), U26.4 (S2), U27.4 (S2), U28.4 (S2), U29.6 (COM), U29.25 (GND)
IMU_CLK: U10.23 (SCL/SCLK), U15.21 (PA5)
IMU_CS: R76.2, U10.8 (nCS), U15.20 (PA4)
IMU_INT: U10.12 (INT), U15.24 (PC4)
IMU_MISO: U10.9 (SDO/AD0), U15.22 (PA6)
IMU_MOSI: U10.24 (SDA/SD1), U15.23 (PA7)
LED_BLUE: R80.2, U15.59 (PB7)
LED_PWR_3V3: C2.1, J2.2, J2.4, J2.6, J2.8, R93.1
LED_STRIP: J26.2, U15.58 (PB6)
unnamed: C5.1, R15.1
unnamed: C61.2, C62.2, R91.1
unnamed: C9.2, D1.1 (K), L1.1, U3.8 (SW)
unnamed: D5.2 (A), R93.2
unnamed: D18.1 (K), R80.1
unnamed: J2.1, U12.5 (VOUT)
unnamed: C10.1, C16.1, J12.3, L1.2, R27.1
unnamed: C9.1, U3.1 (BOOT)
unnamed: C6.1, R15.2, U3.6 (COMP)
unnamed: R27.2, R28.1, U3.5 (FB)
unnamed: R16.1, U3.4 (RT/CLK)
unnamed: U6.5 (CLKIN), Y2.2
unnamed: C62.1, U6.25 (SAG)
unnamed: C60.2, U6.22 (VIN)
unnamed: C61.1, U6.26 (VOUT)
unnamed: U6.6 (XFB), Y2.1
unnamed: C34.1, U10.20 (CPOUT)
unnamed: C33.1, U10.10 (REGOUT)
unnamed: H1.1, R85.2, U14.4 (+)
unnamed: R88.1, U14.6 (OUT)
unnamed: C36.1, U15.5 (PH0), Y1.2
unnamed: C37.1, U15.6 (PH1), Y1.1
unnamed: C38.2, U15.31 (VCAP_1)
unnamed: C39.2, U15.47 (VCAP_2)
unnamed: R4.2, U17.1 (G1)
unnamed: R5.2, U17.5 (G2)
unnamed: R17.2, U18.1 (G1)
unnamed: R18.2, U18.5 (G2)
unnamed: R29.2, U19.1 (G1)
unnamed: R30.2, U19.5 (G2)
unnamed: R43.2, U20.1 (G1)
unnamed: R44.2, U20.5 (G2)
unnamed: R56.2, U21.1 (G1)
unnamed: R57.2, U21.5 (G2)
unnamed: R66.2, U22.1 (G1)
unnamed: R67.2, U22.5 (G2)
unnamed: R46.2, U23.1 (G1)
unnamed: R47.2, U23.5 (G2)
unnamed: R58.2, U24.1 (G1)
unnamed: R59.2, U24.5 (G2)
unnamed: R68.2, U25.1 (G1)
unnamed: R69.2, U25.5 (G2)
unnamed: R7.2, U26.1 (G1)
unnamed: R8.2, U26.5 (G2)
unnamed: R19.2, U27.1 (G1)
unnamed: R20.2, U27.5 (G2)
unnamed: R31.2, U28.1 (G1)
unnamed: R32.2, U28.5 (G2)
OSD_CS: U6.8 (CS), U15.50 (PA15)
OSD_VIDEO_IN: C60.1, J9.3, R39.1
OSD_VIDEO_OUT: J9.2, R91.2
RCIN_INT: J7.2, U15.61 (PB8)
RSSI_IN: C43.1, J7.3, R89.1
SENS_CUR: C47.1, R88.2, U15.9 (PC1)
SENS_RSSI: J4.2, R89.2, U15.14 (PA0)
SENS_VBUS: R77.2, R78.1, U15.25 (PC5)
SENS_VOL: C46.1, R84.2, R86.1, U15.10 (PC2)
SPI2_CLK: J1.2, U15.34 (PB13)
SPI2_CS: J1.1, U15.33 (PB12)
SPI2_MISO: J1.3, U15.35 (PB14)
SPI2_MOSI: J1.4, U15.36 (PB15)
SPI3_CLK: U6.10 (SCLK), U13.4 (SCK), U15.51 (PC10)
SPI3_MISO: U6.11 (SDOUT), U13.5 (SDO), U15.52 (PC11)
SPI3_MOSI: U6.9 (SDIN), U13.3 (SDI), U15.53 (PC12)
STM32_CLK: J5.3, U15.49 (PA14)
STM32_DIO: J5.2, U15.46 (PA13)
STM32_NRST: J5.4, R83.2, U15.7 (NRST)
STM32_PA1: J4.3, U15.15 (PA1)
STM32_PB10: J15.2, R82.2, U15.29 (PB10)
STM32_PB11: J15.3, R81.2, U15.30 (PB11)
UART1_RX: J14.2, U15.43 (PA10)
UART1_TX: J14.3, U15.42 (PA9)
UART6_RX: J8.3, U15.38 (PC7)
UART6_TX: J8.2, U15.37 (PC6)
USB_D+: J20.3 (D+), U15.45 (PA12)
USB_D-: J20.2 (D-), U15.44 (PA11)
V_BAT: C3.1, C4.1, R85.1, R86.2, U3.2 (VIN), U14.5 (-), U17.2 (D1), U18.2 (D1), U19.2 (D1), U20.2 (D1), U21.2 (D1), U22.2 (D1), U23.2 (D1), U24.2 (D1), U25.2 (D1), U26.2 (D1), U27.2 (D1), U28.2 (D1)

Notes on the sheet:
VOL-CUR-RSSI
ESC1
BMP280
ESC4
RESOURCE
CONNECTOR
7.4V~60V
ESC PROG
MPU6000
MOTOR
ESC3
Imax 5A
ESC2
OUTLINE
POWER
OSD
USB
STM32F405RG

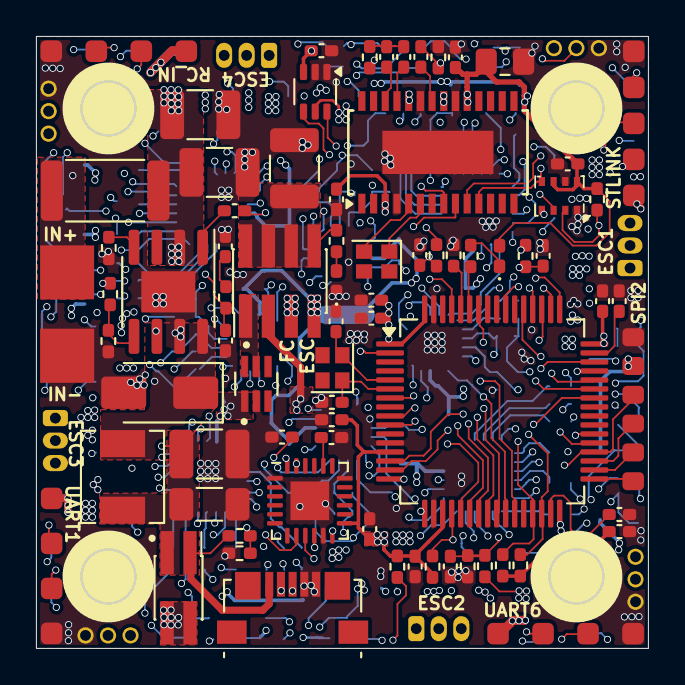
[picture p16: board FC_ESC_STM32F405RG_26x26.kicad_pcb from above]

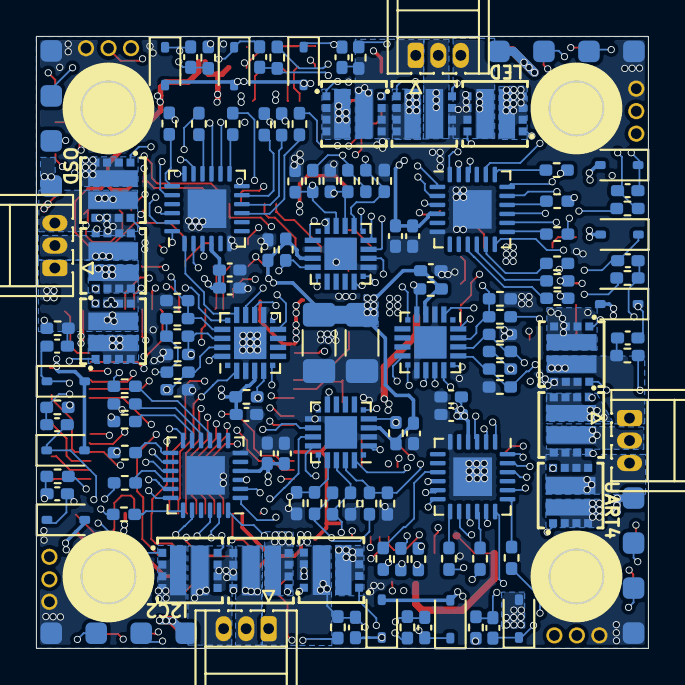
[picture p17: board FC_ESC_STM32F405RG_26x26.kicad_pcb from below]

Board: 8 copper layers, 34.0 x 34.0 mm, 211 parts (130 on the bottom side), 194 nets.

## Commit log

2023-10-15 add ESC and STM32F405RG
    [FC_ESC_STM32F405RG_26x26.kicad_pcb, FC_ESC_STM32F405RG_26x26.kicad_sch]
2023-10-18 update project
    [FC_ESC_STM32F405RG_26x26.kicad_sch]
2023-10-20 update current-voltage measure
    [FC_ESC_STM32F405RG_26x26.kicad_sch]
2023-10-21 update pcb
    [FC_ESC_STM32F405RG_26x26.kicad_pcb, FC_ESC_STM32F405RG_26x26.kicad_sch]
2023-10-22 update placement
    [FC_ESC_STM32F405RG_26x26.kicad_pcb, FC_ESC_STM32F405RG_26x26.kicad_sch]
2023-12-10 update schematic
    [FC_ESC_STM32F405RG_26x26.kicad_sch]
2023-12-11 update routing
    [FC_ESC_STM32F405RG_26x26.kicad_pcb]
2024-01-06 add dimension
    [FC_ESC_STM32F405RG_26x26.kicad_pcb]
2024-03-02 upgrade to Kicad v8
    [FC_ESC_STM32F405RG_26x26.kicad_pcb, FC_ESC_STM32F405RG_26x26.kicad_sch]
2024-03-02 update setting for export BOM
    [FC_ESC_STM32F405RG_26x26.kicad_sch]
2024-03-02 add BOM
    [FC_ESC_STM32F405RG_26x26.xlsx]
2024-03-02 add BOM download link
2024-03-02 update 3d model
    [FC_ESC_STM32F405RG_26x26.kicad_pcb]
2024-03-02 add download gerber
2024-03-02 change origin
    [FC_ESC_STM32F405RG_26x26-B_Cu.gbr, FC_ESC_STM32F405RG_26x26-B_Mask.gbr, FC_ESC_STM32F405RG_26x26-B_Paste.gbr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]
2024-03-02 update BOM
    [FC_ESC_STM32F405RG_26x26.xlsx]
2024-03-02 update symbol value
    [FC_ESC_STM32F405RG_26x26.kicad_sch]
